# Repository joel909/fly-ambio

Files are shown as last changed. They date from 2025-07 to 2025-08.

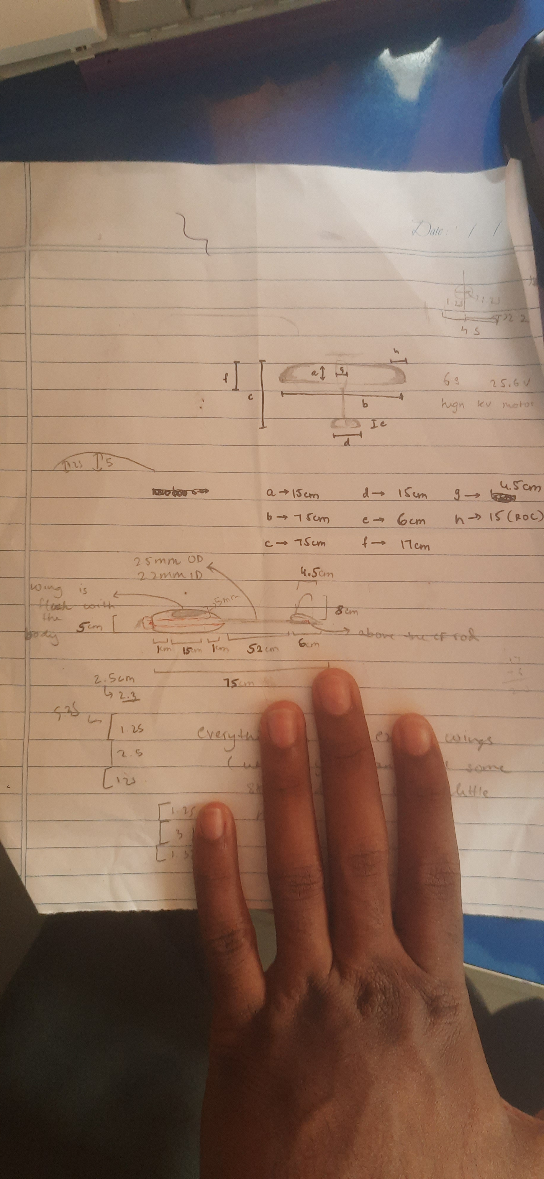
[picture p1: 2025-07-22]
20250722_164915.jpg

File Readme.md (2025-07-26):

# flyambio

#what is fly-ambio
It is a rc controlled plane which can fly over 300km/h planned it has a very aerodynamic desgin and hopes to break the 300km/h speed barier as well hope full i break it !!

Okay so The reason i built this was I love avation in general my fav jet is f-35 i love the tech it has and how fast it can fly as well obv there are more which can go faster but nothing actaully has the tech as in f-35 and flying is just sooo cool imagine a megaa ton mody lifting flying 10000s for feet in the sky when i can baerly get my legs off the ground for jumping
so To make something ive always loved wating vids about i decided to make one

#THe Journey 
it took so long from knowing nothing to knowing everything about the planes i leart a lot iterated a lot and made something great so it was endless problems issue and overcoming issue below I am present yall with the pics of things which i tool to remind my self of the journey 
and below are rought sketcehd







BLEOW IS MY COOL 3D model pics some old some new



FAILED WING DESING I WAS TALKING ABOUT READ JOURNAL.MD


fixed it :)






## 🧾 Bill of Materials (BoM)

| Sl No | Name | Link | Quantity | Total Price (INR) | Total Price (USD) |
|---|---|---|---|---|---|
| 1 | battery 6s 1100mah | [Link](https://rcmumbai.com/products/cnhl-black-series-1100mah-22-2v-6s-100c-lipo-battery-xt60) | 1 | 1977 | 23.72 |
| 2 | battery cahgrer modules | [Link](https://www.flyrobo.in/tp4056-1a-li-ion-lithium-battery-charging-module-with-current-protection-type-c) | 7 | 126 | 1.51 |
| 3 | 5v power supplies for the charger modules | [Link](https://quartzcomponents.com/products/5v-2a-circuit-switch-power-supply-module-smps-pcb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) | 6 | 552 | 6.62 |
| 4 | servo motors | [Link](https://flyrobo.in/mg90s_metal_gear_micro_servo_for_rc_model?search=MG90S&description=true) | 4 | 820 | 9.84 |
| 5 | esc | [Link](https://www.flyrobo.in/readytosky-80a-2-6s-brushless-esc?search=esc+80a&description=true) | 1 | 1870 | 22.44 |
| 6 | motor | [Link](https://www.drkstore.in/t-motor-f80-pro-1900kv-2200kv-2500kv/) | 1 | 2500 | 30.00 |
| 7 | transmitter ELRS | [Link](https://rcmumbai.com/products/radiomaster-pocket?variant=50865323180313) | 1 | 6300 | 75.60 |
| 8 | ELRS reciver | [Link](https://www.drkstore.in/geprc-elrs-nano-915m-v2-receiver/) | 1 | 1499 | 17.99 |
| 9 | flight controller | [Link](https://rcmumbai.com/products/speedybee-f405-wing-app-fixed-wing-flight-controller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) | 1 | 4063 | 48.76 |
| 10 | GPS | [Link](https://www.drkstore.in/tbs-m10q-gps-glonass/) | 1 | 1799 | 21.59 |
| 11 | foam | [Link](https://www.vortex-rc.com/product/5mm-depron-30x20-10-sheet-pack-now-in-india/) | 1 | 1660 | 19.92 |
| 12 | carbon fiber rod | [Link](https://www.vortex-rc.com/product/25x22x1000mm-3k-cf-tube-carbon-fiber-tube-3k-roll-wrapped/) | 1 | 2465 | 29.58 |
| 13 | carbon fiber spar | [Link](https://www.vortex-rc.com/product/5x1000mm-cf-rod-2-pcs-carbon-fiber-rods/) | 1 | 999 | 11.99 |
| 14 | rod holder for carbon fiber | [Link](https://www.vortex-rc.com/product/aluminum-c-clamps-for-carbon-fiber-rods-and-tubes-in-multiple-sizes/) | 1 | 219 | 2.63 |
| 15 | glue, brown paper, 16awg wires, solder, screws | - | - | 500 | 6.00 |
| 16 | fpv camera | [Link](https://www.drkstore.in/caddx-ant-lite-1200tvl-fpv-camera/) | 1 | 1599 | 19.19 |
| 17 | vtx | [Link](https://www.drkstore.in/iflight-blitz-force-5-8ghz-600mw-adjustable-vtx/) | 1 | 3599 | 43.19 |
| 18 | vrx | [Link](https://rcmumbai.com/products/rc-805-5-8ghz-8-channel-av-receiver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) | 1 | 2000 | 24.00 |
| 19 | shipping flyrobo | shipping costs on fly robo | 1 | 100 | 1.20 |
| 20 | shipping quartz components | shipping costs on quartz components | 1 | 50 | 0.60 |
| 21 | shipping rc mumbai | shipping costs on rc mumbai | 1 | 150 | 1.80 |
| | **TOTAL** | | | **34847** | **418.16** |

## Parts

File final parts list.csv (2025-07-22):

sl no | name | link | quantity | total price (INR) | total price (USD)
1 | battery 6s 1100mah | https://rcmumbai.com/products/cnhl-black-series-1100mah-22-2v-6s-100c-lipo-battery-xt60 | 1 | 1977 | 23.72
2 | battery cahgrer modules | https://www.flyrobo.in/tp4056-1a-li-ion-lithium-battery-charging-module-with-current-protection-type-c | 7 | 126 | 1.51
3 | 5v power supplies for the charger modules | https://quartzcomponents.com/products/5v-2a-circuit-switch-power-supply-module-smps-pcb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 | 6 | 552 | 6.62
4 | servo motors | https://flyrobo.in/mg90s_metal_gear_micro_servo_for_rc_model?search=MG90S&description=true | 4 | 820 | 9.84
5 | esc | https://www.flyrobo.in/readytosky-80a-2-6s-brushless-esc?search=esc+80a&description=true | 1 | 1870 | 22.44
6 | motor | https://www.drkstore.in/t-motor-f80-pro-1900kv-2200kv-2500kv/ | 1 | 2500 | 30
7 | transmitter ELRS | https://rcmumbai.com/products/radiomaster-pocket?variant=50865323180313 | 1 | 6300 | 75.6
8 | ELRS reciver | https://www.drkstore.in/geprc-elrs-nano-915m-v2-receiver/ | 1 | 1499 | 17.99
9 | flight controller | https://rcmumbai.com/products/speedybee-f405-wing-app-fixed-wing-flight-controller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 | 1 | 4063 | 48.76
10 | GPS | https://www.drkstore.in/tbs-m10q-gps-glonass/ | 1 | 1799 | 21.59
11 | foam | https://www.vortex-rc.com/product/5mm-depron-30x20-10-sheet-pack-now-in-india/ | 1 | 1660 | 19.92
12 | carbon fiber rod | https://www.vortex-rc.com/product/25x22x1000mm-3k-cf-tube-carbon-fiber-tube-3k-roll-wrapped/ | 1 | 2465 | 29.58
13 | carbon fiber spar | https://www.vortex-rc.com/product/5x1000mm-cf-rod-2-pcs-carbon-fiber-rods/ | 1 | 999 | 11.99
14 | rod holder for carbon fiber | https://www.vortex-rc.com/product/aluminum-c-clamps-for-carbon-fiber-rods-and-tubes-in-multiple-sizes/ | 1 | 219 | 2.63
15 | glue, brown paper, 16awg wires, solder, screws | - | - | 500 | 6
16 | fpv camera | https://www.drkstore.in/caddx-ant-lite-1200tvl-fpv-camera/ | 1 | 1599 | 19.19
17 | vtx | https://www.drkstore.in/iflight-blitz-force-5-8ghz-600mw-adjustable-vtx/ | 1 | 3599 | 43.19
18 | vrx | https://rcmumbai.com/products/rc-805-5-8ghz-8-channel-av-receiver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 | 1 | 2000 | 24
19 | shipping flyrobo | shipping costs on fly robo | 1 | 100 | 1.2
20 | shipping quartz components | shipping costs on quartz components | 1 | 50 | 0.6
21 | shipping rc mumbai | shipping costs on rc mumbai | 1 | 150 | 1.8
 | TOTAL |  |  |  | 418.17

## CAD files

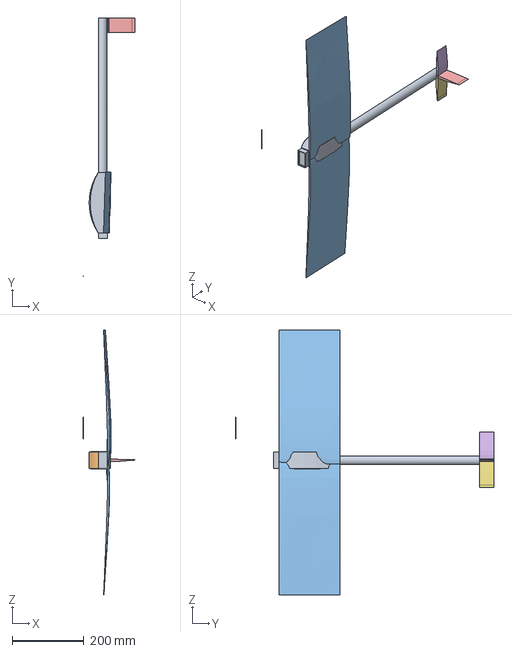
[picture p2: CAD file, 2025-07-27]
plane-model-step.step
145.0 x 721.3 x 740.1 mm

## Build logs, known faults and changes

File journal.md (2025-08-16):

# Journal
---
title: "FlyAmbio"
author: "Joel Joby"
description: "A basic Plane which flies 300km/h"
created_at: "2024-03-20"
---

**TOTAL TIME SPENT OFFICIALLY: 40 Hours**

**TOTAL TIME SPENT unofficially: 80+ Hours**

^ includes those extra lunch breaks at school just looking for improvements!

```hour 1 and 2```

Today I decided to finally build something for hackclub highway so I went up and got a few ideas 

I already had a faint idea in mind, something related to rc... guess I never grew up from those toy rc cars eh?

But ofc, there isnt any fun in just building something someone else has already made, so I needed something new. 

I found [THIS](https://www.youtube.com/watch?v=vljy3lKIN-0) video online, and the brain wave ABOSLUTLY BLEW MY MIND. I knew what I wanted to make
I was gonna make an rc Plane. but not just any rc plane, I wanted to beat what was conventionally thought. I wanted to go FAST. 500kmph to be exact!

So I started my research, but looks like 500 kmph, was not exactly feasible to make on the budget that I had! 
Then I came accross [250km/h, Under 250 Grams V2
](https://lukeattubato.com/250kmh-under-250g-v2)
This was the first grounding source that I had, fully verified, and with a lot on info on how it was made. This was the starting point. The goal also had been moved slighly by now, targetting a speed of 300kmph (luke from the link above). I went though it throughly, and absorbed all the info that I could, learning from the mistakes he made, and what worked best for him. 

```hour 3-4```

on luke's website, he mentioned that his biggest inspiration was this guy called [MikeRX on RCgroups.com](https://www.rcgroups.com/forums/showthread.php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). This source turned out to be an absolute GOLD mine. He not only mentioned what he made, and what works, (This guy had been making these planes for YEARS), but the user interaction from other users there meant that every small detail that he missed was asked/mentioned by another user there. I had 1334 posts to go through. If I was going to make this plane, I needed to learn from the best, and MikeRX did look to be really good at what he did. 

```hour 5```

There was a LOT more info that I had anticipated, and took me a little more time to go through it that what I had expected. decided to finish reading it up, (there was another guy learning from mike's builds, so he had some usefull info int he same thread aswell), and then begin designing my own version of this daemon class rc plane!

# ``` ---> THE ELECTRONICS AND PROPULSION SYSTEMS```
```hour 6 and 7```
> So the first thing I need to figure out is the propulsion system. Did quite a bot of research, took me a while to get a hang of it. Turns out, unlike drone, propultion works  alot differently in planes. SInce they move so much all the time, 2 factors come into play. 
1. the static thrust
2. the top speed

>Static thrust gives us acceleration and is goverened by the rom of the motor, while the top speed depends on the "pitch" of the propeller, which is how much the plane moves forward per rotation of the propeller. If you have too much pitch, the motor will be overloaded for not being able to provide enough torque, will spin slower, and will burn, but if you have too little pitch, then the plane will have a very slow top speed. I have to find a balance between these 2, and find a motor that can take maximum load without heating too much. 

```hour 8```
>Then I figured out fianlly what the Kv rating on a motor really meant! It gave us the unloaded rpm of the motor per volt!
>A little browsing later, I had found what motor I needed. The F80Pro, rated at a whooping 1.2 Kwh!. It had a proven track record from [Drl's racer x drone](https://www.drl.io/racerx), But there was a catch. It was not availible at 2500 Kv anywhere in india. out of stock everywhere(almost). One site did have them, robokits on preorder, but they didnt accept international cards. So i had to settle for the iFlight XING 2203.5 motor, which was similar. I decided to give a call to robokits india afterall, and they had a new pellet of shippments ariving soon, and they told me they could add F80Pro motors on it on a special request. I decided that I would figure out the paying part later, and placed the order for the motors. 

```hour 9```
>Now that I had my motor decided, I had to find a good battery for it. Now this was very tricky. I had understood from mike and luke's posts that I needed atleast a 6s battery, meaning 25.2 nominal voltage, so that I could sping the motor to around 43000 rpm loaded. But these battries where hard to find. We need LiPo battries to get the maximum current, while being light. however, finding sites who sold these battries from repulatble sellers, and also accepted american cards was a piece of work... Finally found one that works for me, and decided to go with it, a 1100mah 6s battery, capable of delivering 110 Amps bursts. at 25.5v. should be able to handle what we throw at it easily. 

```hour 10```
>I already had in mind what flight controller I would use, had come accross it while searching for battries, so that was good I was goign to use a speedybee f405 wing running INAV to stabalise that plane, and make it easier to fly. also added servos while I was at it, but had to change the servos a little later for ones that could take more load, isnce we were going pretty darn fast.

```hour 11 and 12```
> I needed a GPS module now, to keep track if it got lost. there were a lot of options, but most of them were far to expensive to make sense. FInally I did find one that ran a slightly old algorithim, but if it works, it work!
> Had to get a way to talk to the plane, ofcourse, so I chose ELRS firmware based RX and TX units. They are very popular, and have known relaiability, and not too expensive like DJI systems. Sounds perfect. Finally found a rx and tx for my elrs setup, the cheapest I could find that still worked for my usecase. 

```hour 13 an 14 and 15```
Yes. You read it right. It actually took me more than 3 hours to find the right propeller, but I will only log 3 here. 
> I first went to mike and luke's blog to see what propeller size and pitch to use. also ran quite a few text based sims to find the optimal pitch so I can reach the target speed, and the right diameter so i dont overload the motor and burn it.
Finally settled with a 5x5 propeller, meaning 5 inch diameter, and 5 inch pitch. I will later modify this propeller like how I had learnt in those blogs to make it a 4x5 propeller and recude the load furthur.

```hour 16 and 17```
> WHY DOES NO ONE WANT TO SELL/MAKE GOOD PROPELLERS IN INDIA???
> FPV dosent have a very big market in india, so there arnt really many people who make and sell these propellers that I need. now keep in mind, I cant just use a normal plastic propeller. at 43000 rpm, a propeller will be experiencing a LOT of centrifugal force on it.
> as adviced and proved by mike, I needed a good propeller made from polycarbonate( similar to carbon fiber, but a composite using other materials along with carbon fiber).
> I wanted APC or German prop propellers since they are good reliable companies, but I had to settle for some locally sourced onces, since not a lot of sellers seem to import those proppellers into india, for the lack of market for them.

```hour 18 and 19``` 
> Now that I had most of the powersystem in place, I could finally look at some prospective escs to run the bldc motor, since these motors required a 3 phase AC input rather than a simple DC, so make them more efficient, run at higher rpms, and take that title of being drone motors!
> I decided to take into account that its going to go througha  lot of crashes initially, and I need a reliable escs that can take those hits. There were only 2 good choices, since we needed racing escs to be able to 
1. handle 6s
2. handle the intense stress of moving a prop with sunch a huge pitch
3. be very responsive and fast, since at those speeds, a second of delay is around 83 meters propelled forward.

>These escs were however very expensive. So I found an alternative, I found out that DRL had a branch in india called IDRL, and they had a MASSIVE store of second hand parts! unfortuanatly most of the parts are made for drones, but I did manage to find Formula f45 Emax racing escs imported from USA, barely used, which were perfect for the job. 

```hour 20```
>Now I needed the basic materials to make the plane. I searched a lot, but either sites were selling the materials at EXORBITANT prices, or they simply did not keep them in stock. I even called a couple of the biggest manufactures in india and asked the materials, but they refused to sell such small quantities of foam, balsa and other parts that I needed. However, when almost all hope was lost, thanks to a couple of active redditors, I came accross [vortex rc](https://www.vortex-rc.com/), and they seemed to have practically all I needed to make the body, including the carbon fiber rods, at veyr good prices.

```hour 21```
> I spent the next hour just finding the other small things that I needed to make the plane, some epoxy, 16 AWG silicon wires, XT60 connectors, brown paper at 150gsm, some nylon screws, solder, etc. I wanted to make sure I wasent forgetting anything.

```hour 22 and 23```
> Now for the fun part! (not so much)
> One thing that was COMPLETELY new in my design, was that no one else seemed to have been putting FPV into their planes, purely to save on weight. but with that bigger battery, I could afford to put in 20ish grams more without loosing too much speed. 
> I needed to however save as much money on these as possible, as the plane was already getting rather pricy. So i sacrifisede quality a little bit, and went forthe chespest parts I could find. This took QUITE a while, since I had 2 objectives to clear
1. finding the cheapest possible parts
2. Finding them on sites thats accept international cards.

>overall, I think I did alright with the electroinics and the propultion systems. 

>as per requirements, I make a couple of schematics on how everyting will be connected together as a schematic

INSERT IMAGE HERE

# ``` --->   THE OVERALL DESIGN```

```hour 24 and 25```
>Now that I had the size of my parts, I need to figure out,  what is the overall dimentions of the entire thing? Again, Mike's blog is plently usefull, but I want to try something new. I want to add a slightly bigger battery for more flight time, and make it more durable, since his balsa planes would absolutly shatter apon impact, and i am still a rookie flyer. 

INSERT IMAGE HERE

>Phew! That definitly took a lot longer that I wanted it to, but I want to get it right the first time round...

>I now have a basic idea of how my plane is gonna look, and its starting to show!
This step has required me to use the free credits from not just 1, but 2 chatGPT free accounts, to Verify is it looks about ok, and for making the frontal area and wing area calculations faster, since chatgpt is sooo good at math, definitly dosent halucinate all the time ;)
asked chatgpt to run a couple of sims aswell to see how well it thinks the plane would perform, and made a few tweaks according to suggestions.

>**I will take my design to a friend at school who has made something similar later, just to get that final satisfaction that it will fly.**

>```I know I verify too much, but i'm a measure twice cut once typa guy!```

>spoiler alert, this is NOT going to be the last time I have to modify the design...

>Got my design vetted by the frined at school, looks like its ready to proceed with the next step!

# ``` --->   THE MAIN WING```
```hour 26```
>Mike mentioned that he had sanded down his airfoil manually, but while that worked for him, I wanted to get this thing done the right way so took a couple lessons from chatGPT, and after verifying from a few more sources online, looks like MH-43 is going to be the perfect choice for this build. its thin, got low lift, very little frontal area, and super efficint at high speeds. as I said, perfect. 
Verified from the pics Mike sent on scaled mats, and decided to use a modified MH-43 airfoil. I was gonna use a 33% MH-43 airfoil, meaning that the thickness of the wing was going to be 33% of the origical MH-43 airfoil, therefore reducing frontal area, and hence the drag aswell. Found the airfoil at [airfoiltools.com](http://airfoiltools.com/airfoil/details?airfoil=mh43-il)

```hour 27 and 28```
>So now I have to get started on my CAD fo the main wing. I had found my airfoil and I knew the thickness that I needed, but uhh that was about about. So I checked how I can export that airfoil from the website into autodesk fusion 360, and It seems to give me a ```.DAT``` file with just the coordinates for making that airfoil... Oh come on man! wheres the CAD importable file format??? I started to trace the thing out manually instead, but 5 min in and barely anything done, I knew I needed a better way to get this done.

```hour 29 and 30```
>So I did the next logical thing that anyone would do...
I WROTE A AUTODESK PLUGIN JUST TO MAKE THAT AIRFOIL! So I wrote the code, uploaded that file, and clicked on. Belive it or not, IT WORKED! I swear to god I laughed for a solid 2 minuites... It was fianlly done! I now had the outline of the wind that I wanted to make, and it was time to get started on the actual thing!

```hours 31 and 32 and 33```

>I loaded up my file, and extruded that wing. what a beauty! Now I had to cut out the flaps for that wing, curve some corners, and get everything aligned right. 
But ofcourse, nothing is ever just as easy as I want it to be, now, is it? My PC was lagging to a point where moving the mouse too a second... (someone please donate me a GPU UwU)
>I realised half way through my design that it would be more aerodynamic to just strip the curved cylinder like thing and make it flat. That would increase the aerodynamics, and it would have reduced the drag at high speeds. 

```hours 34 and 35```
>OH SOMEONE PLEASE HELP ME!!!
almost threw my house at my laptop. I HAD FORGOTTEN TO GET THAT 33% AIRFOIL FROM AIRFOILTOOLS.COM, AND HAVE TO DO THE ENTIRE WING AGAIN. WHAT SINS DID I COMMIT IN MY PAST LIFE TO HAVE HAD THIS DONE TO ME??? 😭

>So with a very pissed off brain and absolutly no will to make it again, I did it. I made the entire wing again, with all the flaps, all the alignments, all the right corners, and had to go thought all that Lag all over again. suprisingly it look a lot lesser time to make it, since I already knew exactly what I needed to do. 

>In the end, I Finally have my wing ready, but I am too tired to  work more on it for today.

```hours 36 and 37```

> Its a new day, and time to make new mistakes!
I started off with the main fuselage body, and a little while later, the thing was actually starting to look like more than just a plank of wood. It looked like a giant Holy cross! We were finally getting somewhere.

```hours 38 and 39 and 40```
> So I finished the rudder and the horizontal stabalizer, I have the same airfoil for both of them as that of the main wing, it seems perfect, however the stabalizer has a 50% airfoil rather than a 33% as used by the mainwing, since at 33% it was far too thin. Same goes for the rudder wing. I decided not to have a flap on the rudder, as it didnt bring too much stability to the plane at that speeds, and a an extra servo increases weight. 

```hours 41 and 42```
>I put in the rest of the small details into the cad, the front motor, the propeller, and a couple of more details, trying to finish off the 3d model today. 
>Took a little longer than expected, had to work a few small errors in the model, and ofcourse, my PC wasent exactly trying to help me out :) but at this point, we finally have most of the 3d model ready! It looks like an actual plane now! super excited to actually build this now!

```hours 43 and 44```
>looked up more about INAV, the controlling firmware for our build, to help with getting the plane back if its lost, giving back telementry so I know when the battery is about to die, and ofcourse, to find out the actual speed at which its flying!
>Searched up what settings I needed to enable, and tinkered in their IDE for a while to get familiar with it. 

```hour 45```
>With everything almost ready, I decided to join a couple of discord servers full of people from everywhere, and asked for some tips, made a few tweaks, and looks likes it should now be ready to go!

```hours 45 to 49.5```
>belive it or not, formating and making this Journal too a LOT of time... I have tried to include as many details as possible, and logged all my failures, and successes. Hopefully this makes the cut!

    PS: This turned out to be a LOT of fun, so stay turned for a complete build log aswell!!

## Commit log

2025-06-16 made the sample design day 3 commit
2025-07-22 part list update
    [final parts list.csv]
2025-07-22 stl file for plane
2025-07-22 added BOM to readme
2025-07-27 added plane's model in step
    [plane-model-step.step]
